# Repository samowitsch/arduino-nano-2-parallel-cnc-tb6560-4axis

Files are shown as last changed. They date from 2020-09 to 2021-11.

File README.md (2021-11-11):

# Arduino nano to parallel TB6560 cnc driver board adapter

This is my little Arduino nano to parallel TB6560 cnc driver board project. Started some time
ago using a red TB6560 4-axis board (before that i had an green 3-axis TB6560). 
At the moment the TB6560 alu case version is my preferred choice 
(but over time i can not remember why the red board was annoying me).
The adapter should also work with 3-axis TB6560 boards if the Pinout is the same.

* [KiCad](https://kicad.org/) files are included if you have special needs.
* Gerber files are included if you want to order your own pcb for e.g. at [jlcpcb.com](https://jlcpcb.com/)
* STL file of simple mount plate made with OpenSCAD is included if you have a 3d printer

Just work in progress current revision 1.4 using GRBL 1.1h.

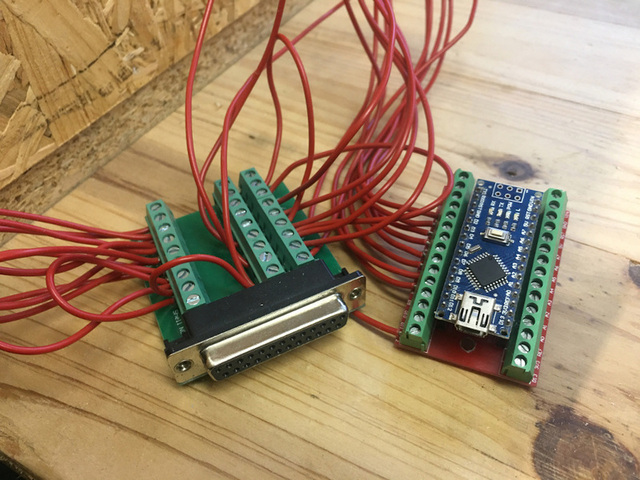
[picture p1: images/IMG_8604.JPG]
First try

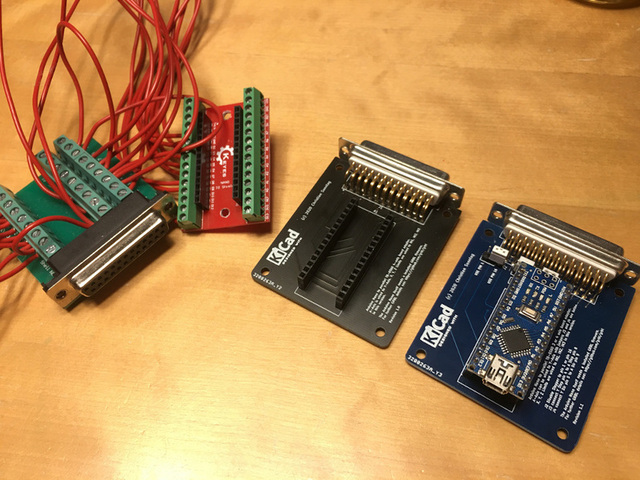
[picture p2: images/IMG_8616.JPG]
Version history

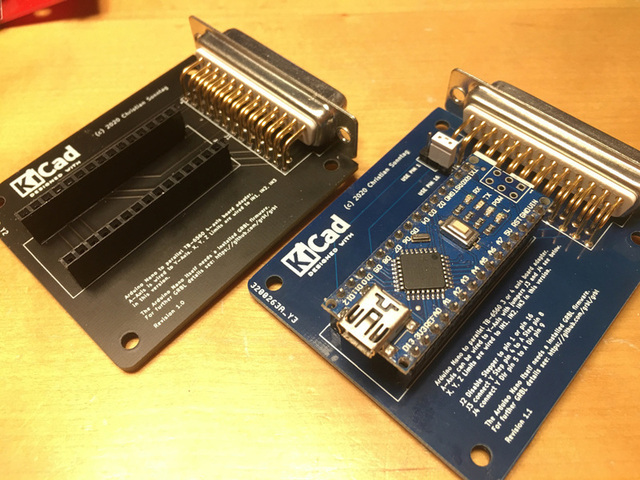
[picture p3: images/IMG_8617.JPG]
Revision 1.0 and 1.1

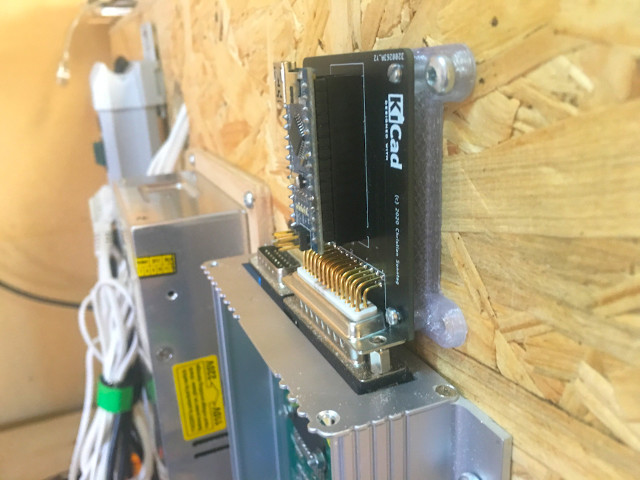
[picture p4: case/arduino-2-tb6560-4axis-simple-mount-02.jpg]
Connected to tb6560 with simple mount

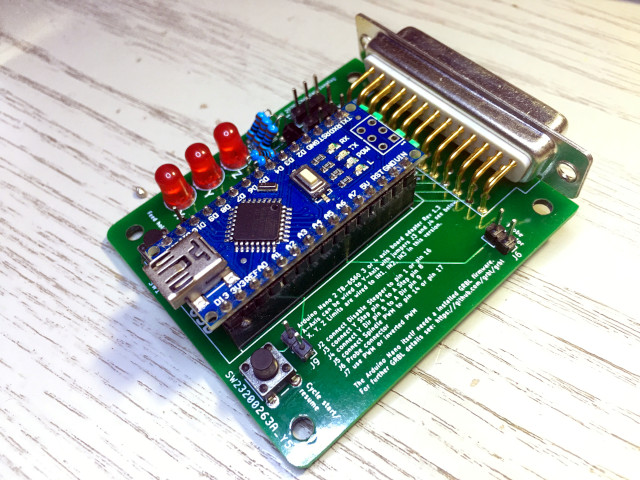
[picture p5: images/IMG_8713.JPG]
Revision 1.3

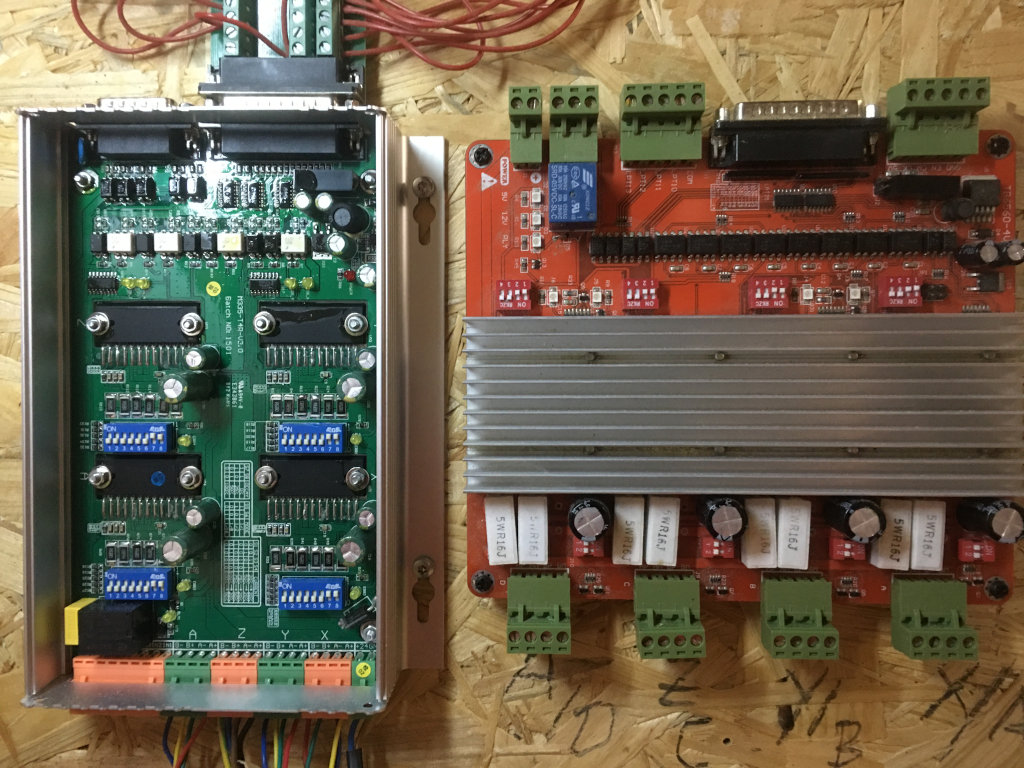
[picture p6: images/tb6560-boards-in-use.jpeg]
Used boards


## Known bugs of rev. 1.3

* holes for resistors are to close for "normal" resistors. my fault this is my first pcb project. i choose a wrong footprint.
* silk outline for X, Y, Z leds on pcb has wrong orientation (my fault or bug in KiCad library?)

## KiCad schema

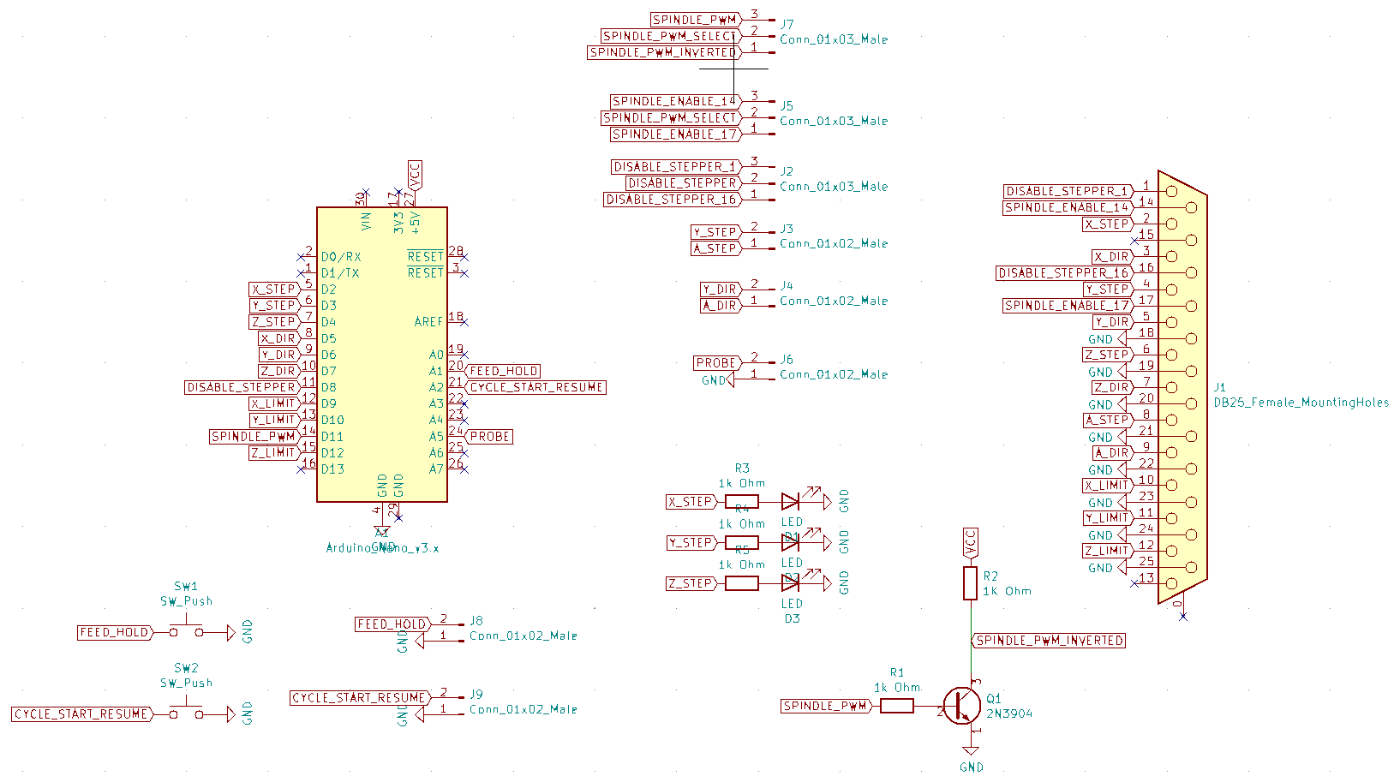
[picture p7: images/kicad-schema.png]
KiCad Schema


## KiCad pcb wiring

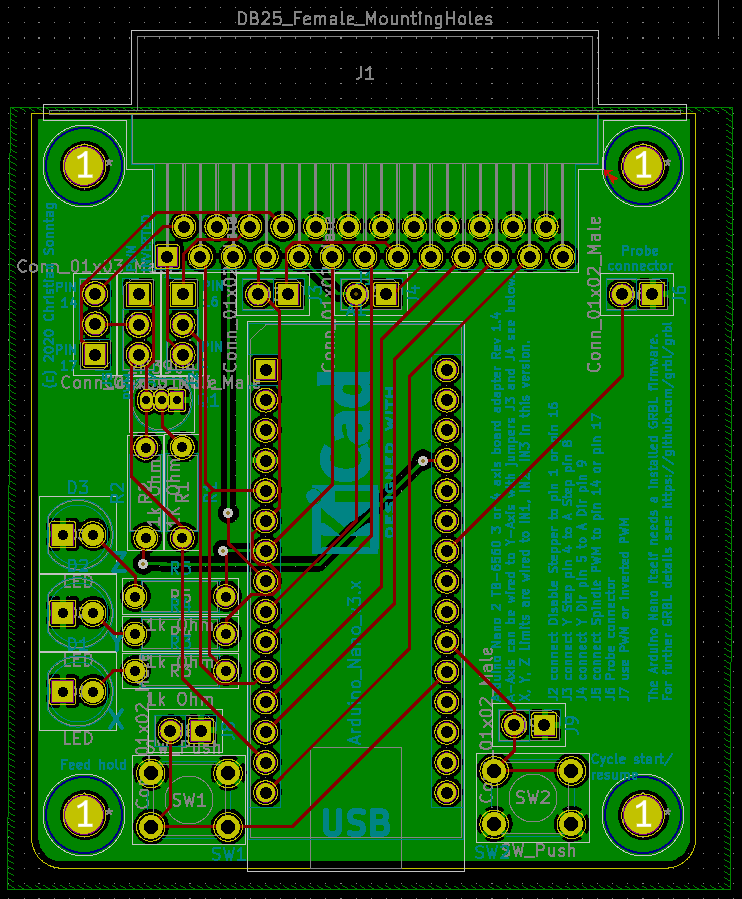
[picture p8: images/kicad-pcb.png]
KiCad pcb wiring


## KiCad pcb 3d preview

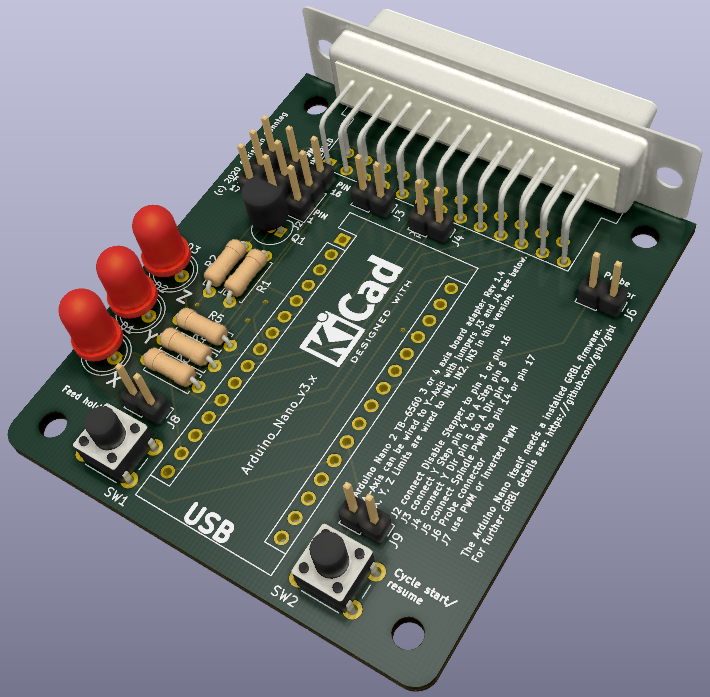
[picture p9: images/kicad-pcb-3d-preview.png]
KiCad pcb wiring


## BOM for revision 1.4

Quantity | Pos | Part
--- | --- | ---
1 | | pcb from pcb manufacturer of your choice
1 | J1 | DSUB-25 female horizontal
5 | R1-R5 | 1k Ohm resistor
1 | Q1 | 2N3904 transistor
2 | SW1,SW2 | tactile push buttons 6x6
3 | D1-D3 | led 5mm
5 | J3,J4,J6,J8,J9 | jumper header 2 pins
3 | J2,J5,J7 | jumper header 3 pins
5 | | jumper
2 | | 15 pin single row female straight header strip 2.54mm pitch for arduino nano

## Simple mount in OpenSCAD

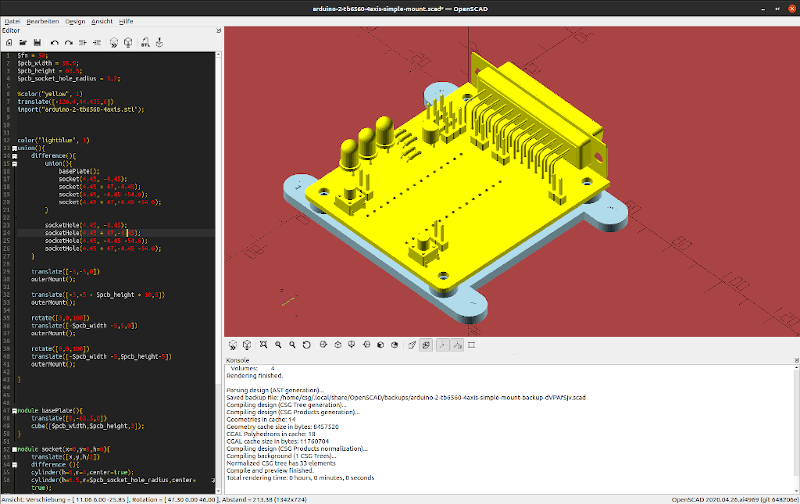
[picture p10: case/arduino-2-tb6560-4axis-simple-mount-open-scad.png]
Simple mount in OpenSCAD


## Revision photos

Picture | Revision | Comment
--- | --- | ---
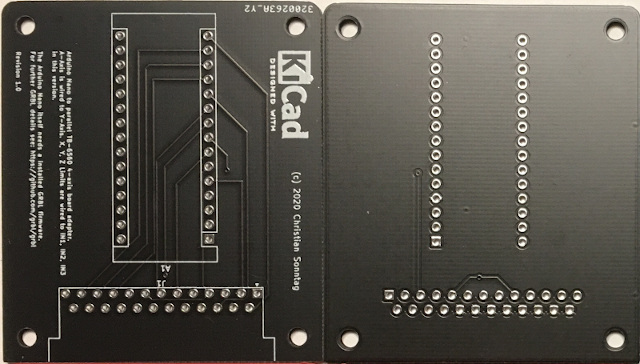
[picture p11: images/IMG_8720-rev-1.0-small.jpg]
 | 1.0 | first dirty revision to get rid of the spaghetti grbl adapter ;o)
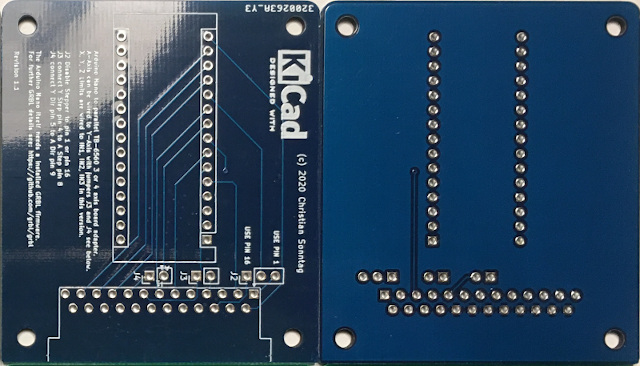
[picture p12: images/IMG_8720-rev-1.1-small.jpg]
 | 1.1 | added jumper headers for the two versions (red pcb, alu case) of the TB6560
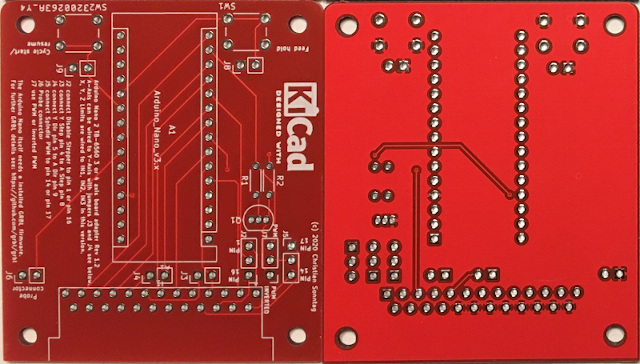
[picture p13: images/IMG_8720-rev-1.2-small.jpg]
 | 1.2 | added two buttons for cycle start/resume and feed hold. added probe connector. added inverter circuit for spindle enable.
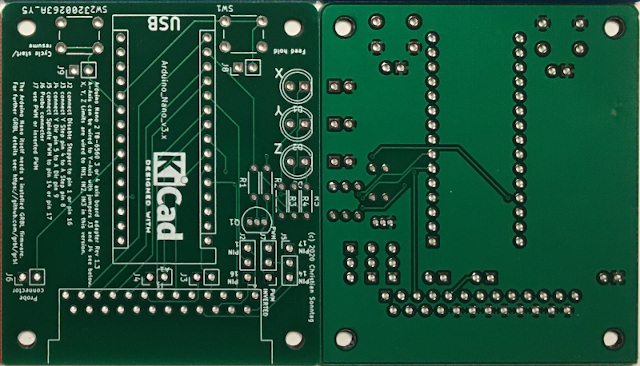
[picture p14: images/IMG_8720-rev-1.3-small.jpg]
 | 1.3 | added leds just for fun.
No real pcb image yet | 1.4 | fix wrong orientation of leds. fix wrong footprint of resistors. reroute affected tracks.

## Pins

Arduino nano | GRBL 1.1 | DB25 red pcb | DB25 alu case version
---|---|---|---
D8 | Disable Stepper | 1 | 16
D2 | X Step | 2 | 2
D3 | Y Step | 4 (+8 A Step) | 4 (+8 A Step)
D4 | Z Step | 6 | 6
D5 | X Dir | 3 | 3
D6 | Y Dir | 5 (+9 A Dir) | 5 (+9 A Dir)
D7 | Z Dir | 7 | 7
D9 | X Limit | 10 (IN1) | 10 (IN1)
D10 | Y Limit | 11 (IN2) | 11 (IN2)
D11 | Spindle Enable | 14 | 17 (see PWM invert!)
D12 | Z Limit | 12 (IN3) | 12 (IN3)
D13 | Spindle Dir | 	 | 
A0 | Reset/Abort | 	 | 
A1 | Feed/Hold | 	 | 
A2 | Cycle Start/Resume | 	 | 
A3 | Cooling Enable | 	 | 
GND | GND | 18-25 | 18-25

## Jumper on board

There are some jumpers to configure the board for the two used 4-axis board versions.

Jumper | Description
---|---
J2 | connect Disable Stepper to pin 1* or pin 16** 
J3 | connect Y Step pin 4 to A Step pin 8
J4 | connect Y Dir pin 5 to A Dir pin 9
J5 | connect Spindle PWM to pin 14* or pin 17**
J6 | Probe connector
J7 | use PWM, inverted PWM or disable (no jumper) 
J8 | connector for alternative feed hold button
J9 | connector for alternative cycle start/resume button

*red board version / **alu case version

## PWM invert

TB6560 boards use low as spindle enable and high as spindel disable (WTF!?). It is the opposite way of how GRBL handle spindle enable/PWM.
The used invert circuit will fix this. But there is a little gap where the invert is not active during startup/shutdown.
> !!! As a workaround for now -> power on arduino at first and power off at last again to prevent injury through spindle.

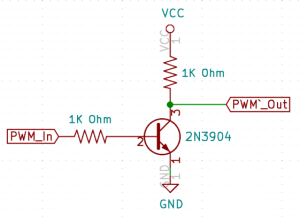
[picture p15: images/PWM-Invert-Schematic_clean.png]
KiCad Schema


Sources: 
* [How to setup inverting PWM signal and using +5v to switch off spindle motor? · Issue #22 · gnea/grbl · GitHub](https://github.com/gnea/grbl/issues/22)
* [GRBL PWM inverter circuit](https://blog.eccentricworkshop.com/grbl-pwm-inverter-circuit/)
* [Explain the Logic NOT Gate or Inverter and its Operation with Truth Table](https://electronicspost.com/explain-the-logic-not-gate-or-inverter-and-its-operation-with-truth-table/)

## My current GRBL settings

```
$$
$0=10
$1=25
$2=0
$3=5
$4=0
$5=0
$6=0
$10=1
$11=0.010
$12=0.002
$13=0
$20=0
$21=0
$22=0
$23=0
$24=25.000
$25=500.000
$26=250
$27=1.000
$30=1000
$31=0
$32=0
$100=402.000
$101=402.000
$102=402.000
$110=1500.000
$111=1500.000
$112=750.000
$120=42.000
$121=42.000
$122=42.000
$130=2000.000
$131=2000.000
$132=2000.000
```

## Probe G Codes

```
G38.2 z-10 f1
```
http://www.linuxcnc.org/docs/2.6/html/gcode/gcode.html#sec:G38-probe
```
G92 z19.2
```
http://www.linuxcnc.org/docs/2.6/html/gcode/gcode.html#sec:G92

## bCNC custom user button

Evaluate gcodes to test with bCNC custom user button.

```text
G38.2 z-100 f5 
G92 z19.7
G0 z50 f600
```

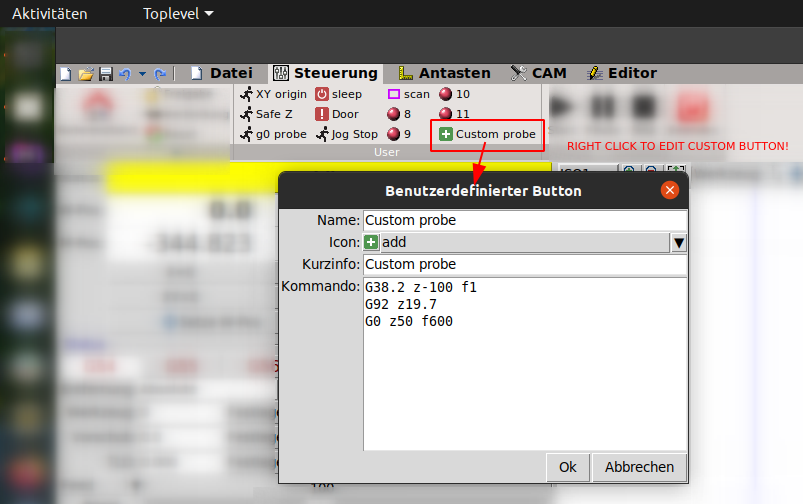
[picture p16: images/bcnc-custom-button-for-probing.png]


## Compiling GRBL

Download, extract and copy GRBL to the Arduino library. More details see here: https://github.com/gnea/grbl/wiki/Compiling-Grbl

Arduino IDE settings:
* Tools -> Board -> "Arduino Nano"
* Tools -> Processor -> "ATmega328P (Old Bootloader)"
* Tools -> Port -> "/dev/ttyUSB0" (may vary)
* Tools -> Programer -> "Atmel-ICE(AVR)"

## Arduino nano pinout

GRBL PWM enabled | GRBL
---|---
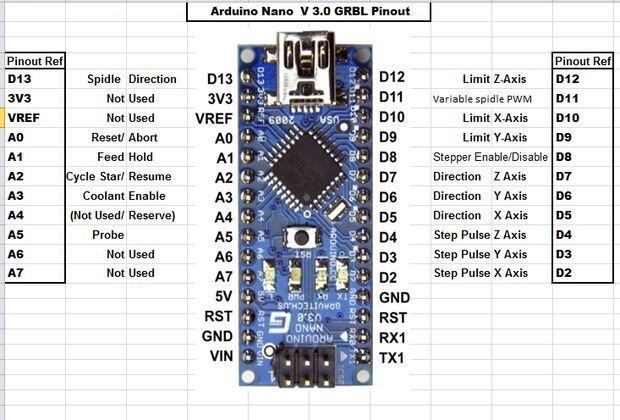
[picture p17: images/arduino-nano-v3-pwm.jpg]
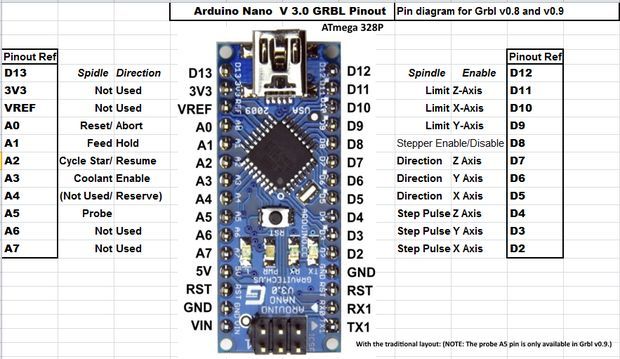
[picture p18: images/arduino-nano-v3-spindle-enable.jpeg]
 | 

### Only for comparison GRBL on STM32F103C8T6 (bluepill)

Just for info. Interesting board with much faster cpu and more memory.  https://github.com/usbcnc/grbl

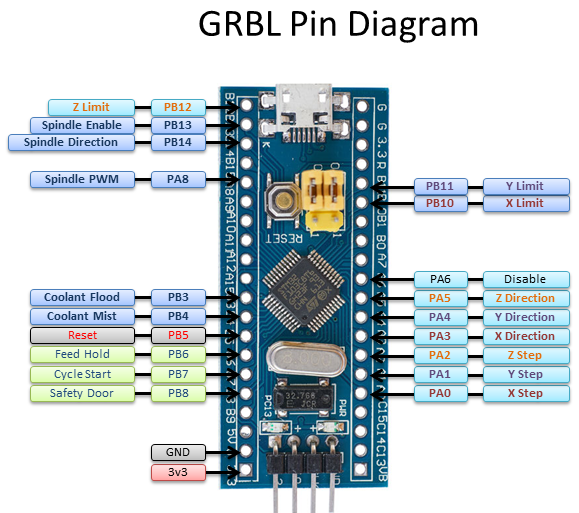
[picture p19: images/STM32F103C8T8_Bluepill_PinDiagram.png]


## other Source
* [Des Fricklers Fräse](https://der-frickler.net/technik/frickelfraese)
* [Make: China-Schrittmotorsteuerung](https://www.heise.de/make/artikel/3-Achs-Schrittmotorsteuerung-aus-China-1518901.html)
* [Grbl CNC USB to TB6560 Interface using Arduino](https://www.coreforge.com/blog/2014/08/grbl-tb6560-interface/)
* [G25 CNC Shield ](http://kclinear.com/G25/Instructions.pdf)

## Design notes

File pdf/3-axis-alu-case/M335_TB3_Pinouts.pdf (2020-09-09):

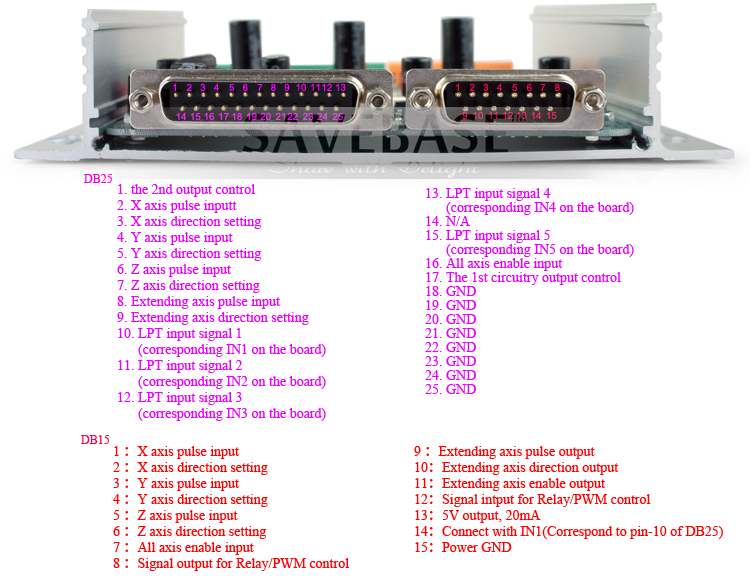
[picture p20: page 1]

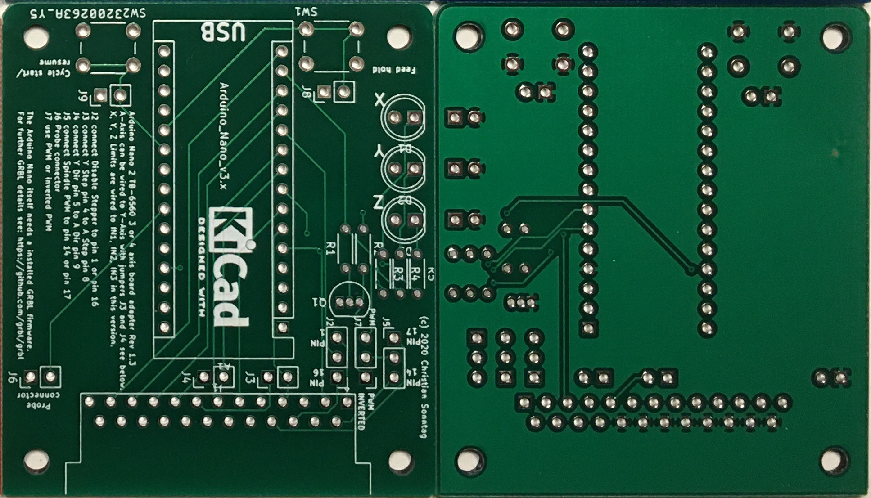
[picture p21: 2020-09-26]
images/IMG_8720-rev-1.3.jpg

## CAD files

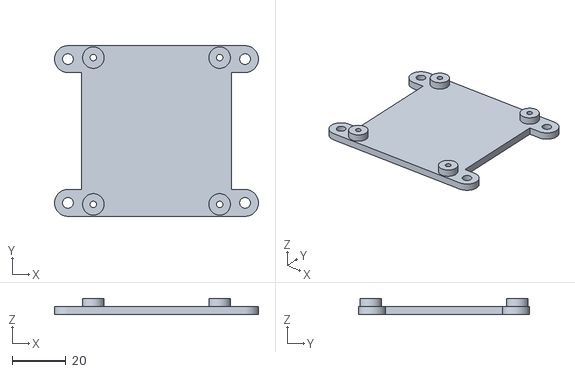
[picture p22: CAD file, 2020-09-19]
case/arduino-2-tb6560-4axis-simple-mount.stl
75.9 x 63.5 x 6.00

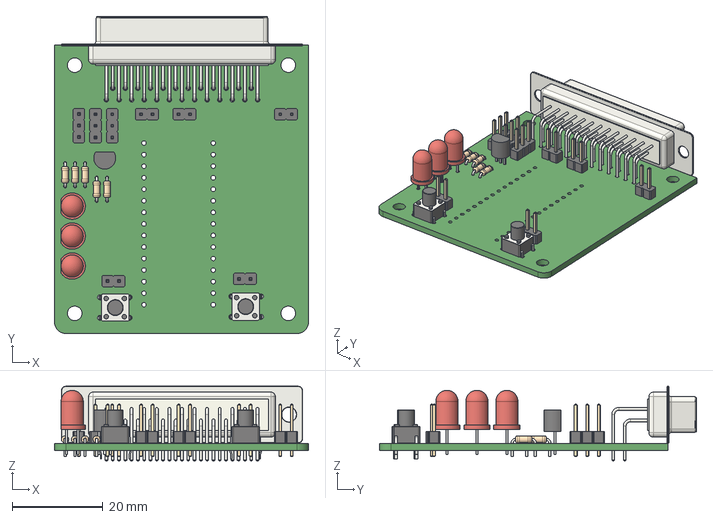
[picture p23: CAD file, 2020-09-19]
case/arduino-2-tb6560-4axis.step
55.9 x 69.8 x 16.4 mm

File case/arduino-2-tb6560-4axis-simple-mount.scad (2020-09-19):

$fn = 50;
$pcb_width = 55.9;
$pcb_height = 63.5;
$pcb_socket_hole_radius = 1.2;

%color("yellow", 1)
translate([-126.4,44.435,6])
import("arduino-2-tb6560-4axis.stl");



color("lightblue", 1)
union(){
    difference(){
        union(){
            basePlate();
            socket(4.45, -4.45);
            socket(4.45 + 47,-4.45);
            socket(4.45, -4.45 -54.6);
            socket(4.45 + 47,-4.45 -54.6);
        }
        
        socketHole(4.45, -4.45);
        socketHole(4.45 + 47,-4.45);
        socketHole(4.45, -4.45 -54.6);
        socketHole(4.45 + 47,-4.45 -54.6);
    }

    translate([-5,-5,0])
    outerMount();

    translate([-5,-5 - $pcb_height + 10,0])
    outerMount();

    rotate([0,0,180])
    translate([-$pcb_width -5,5,0])
    outerMount();

    rotate([0,0,180])
    translate([-$pcb_width -5,$pcb_height-5])
    outerMount();

}



module basePlate(){
    translate([0,-63.5,0])    
    cube([$pcb_width,$pcb_height,3]);
}

module socket(x=0,y=0,h=6){
    translate([x,y,h/2])
    difference (){
    cylinder(h=6,r=4,center=true);
    cylinder(h=6.5,r=$pcb_socket_hole_radius,center=true);
    }
}

module socketHole(x=0,y=0,h=6.5){
    translate([x,y,h/2])
    cylinder(h=h,r=$pcb_socket_hole_radius,center=true);
}

module outerMount(){
    difference(){
        union(){
            translate([0,-5,0])
            cube([5,10,3]);
            cylinder(d=10, h=3);
        }
        cylinder(d=4, h=3);
    }
}

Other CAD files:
case/arduino-2-tb6560-4axis.stl

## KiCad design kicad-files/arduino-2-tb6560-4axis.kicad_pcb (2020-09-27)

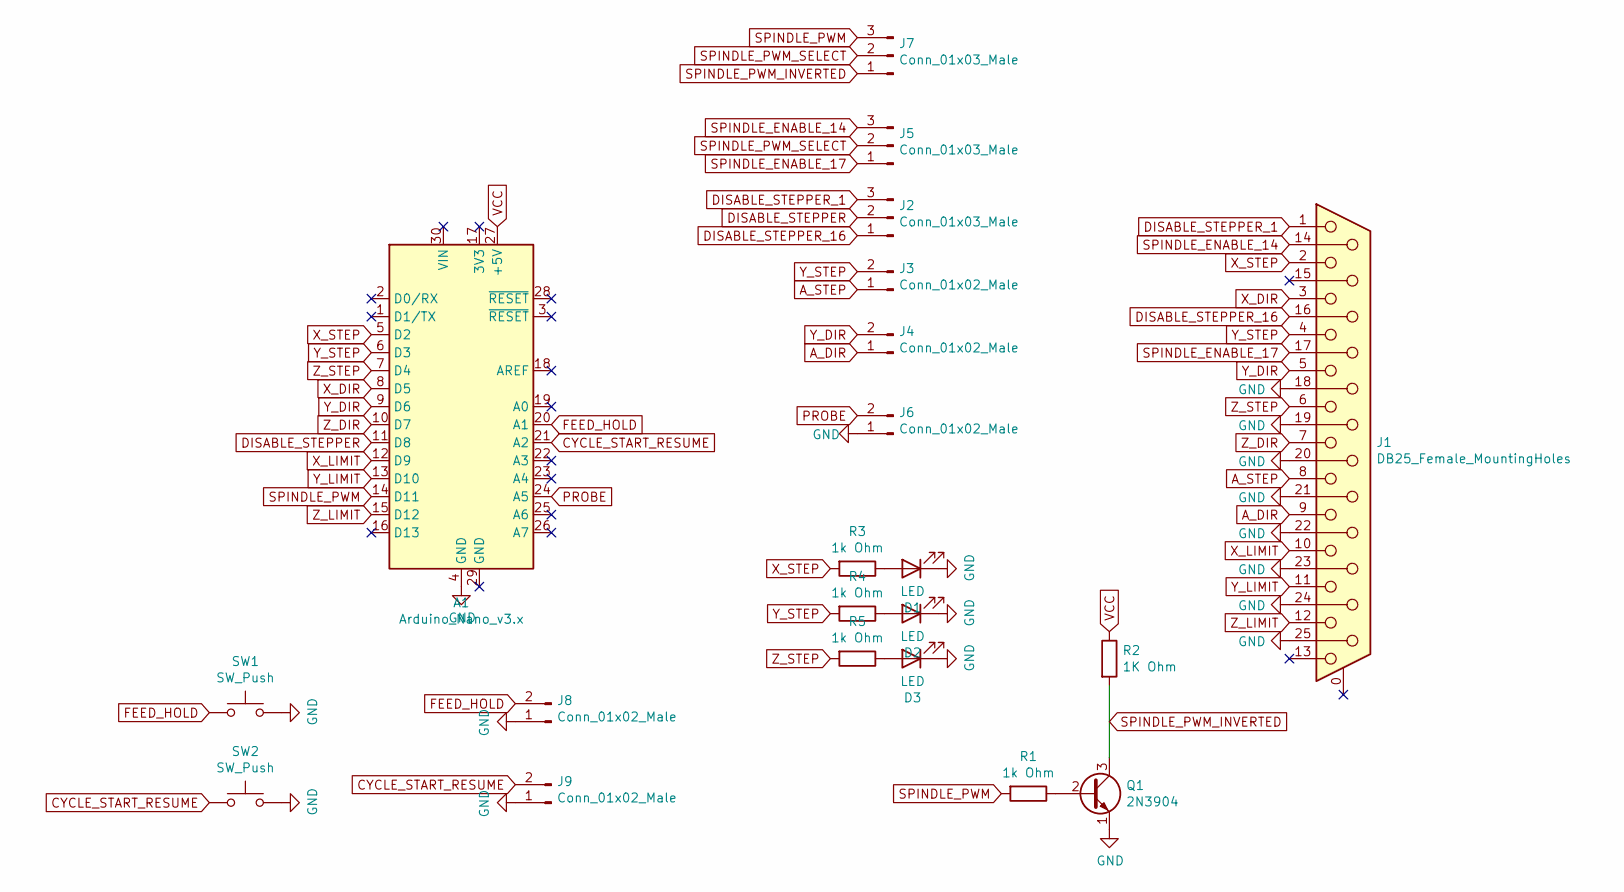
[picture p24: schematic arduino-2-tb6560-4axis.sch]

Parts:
A1: Arduino_Nano_v3.x; Arduino_Nano
D1, D2, D3: LED; LED_D5.0mm
J1: DB25_Female_MountingHoles; DSUB-25_Female_Horizontal_P2.77x2.54mm_EdgePinOffset9.40mm
J2, J5, J7: Conn_01x03_Male; PinHeader_1x03_P2.54mm_Vertical
J3, J4, J6, J8, J9: Conn_01x02_Male; PinHeader_1x02_P2.54mm_Vertical
Q1: 2N3904; TO-92_Inline
R1, R3, R4, R5: 1k Ohm; R_Axial_DIN0207_L6.3mm_D2.5mm_P7.62mm_Horizontal
R2: 1K Ohm; R_Axial_DIN0207_L6.3mm_D2.5mm_P7.62mm_Horizontal
SW1, SW2: SW_Push; SW_PUSH_6mm_H7.3mm

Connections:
A_DIR: J1.9, J4.1
A_STEP: J1.8, J3.1
CYCLE_START_RESUME: A1.21 (A2), J9.2, SW2.1
DISABLE_STEPPER: A1.11 (D8), J2.2
DISABLE_STEPPER_1: J1.1, J2.3
DISABLE_STEPPER_16: J1.16, J2.1
FEED_HOLD: A1.20 (A1), J8.2, SW1.1
GND: A1.4 (GND), D1.1 (K), D2.1 (K), D3.1 (K), J1.18, J1.19, J1.20, J1.21, J1.22, J1.23, J1.24, J1.25, J6.1, J8.1, J9.1, Q1.1 (E), SW1.2, SW2.2
unnamed: D1.2 (A), R3.1
unnamed: D2.2 (A), R4.1
unnamed: D3.2 (A), R5.1
unnamed: Q1.2 (B), R1.1
PROBE: A1.24 (A5), J6.2
SPINDLE_ENABLE_14: J1.14, J5.3
SPINDLE_ENABLE_17: J1.17, J5.1
SPINDLE_PWM: A1.14 (D11), J7.3, R1.2
SPINDLE_PWM_INVERTED: J7.1, Q1.3 (C), R2.2
SPINDLE_PWM_SELECT: J5.2, J7.2
VCC: A1.27 (+5V), R2.1
X_DIR: A1.8 (D5), J1.3
X_LIMIT: A1.12 (D9), J1.10
X_STEP: A1.5 (D2), J1.2, R3.2
Y_DIR: A1.9 (D6), J1.5, J4.2
Y_LIMIT: A1.13 (D10), J1.11
Y_STEP: A1.6 (D3), J1.4, J3.2, R4.2
Z_DIR: A1.10 (D7), J1.7
Z_LIMIT: A1.15 (D12), J1.12
Z_STEP: A1.7 (D4), J1.6, R5.2

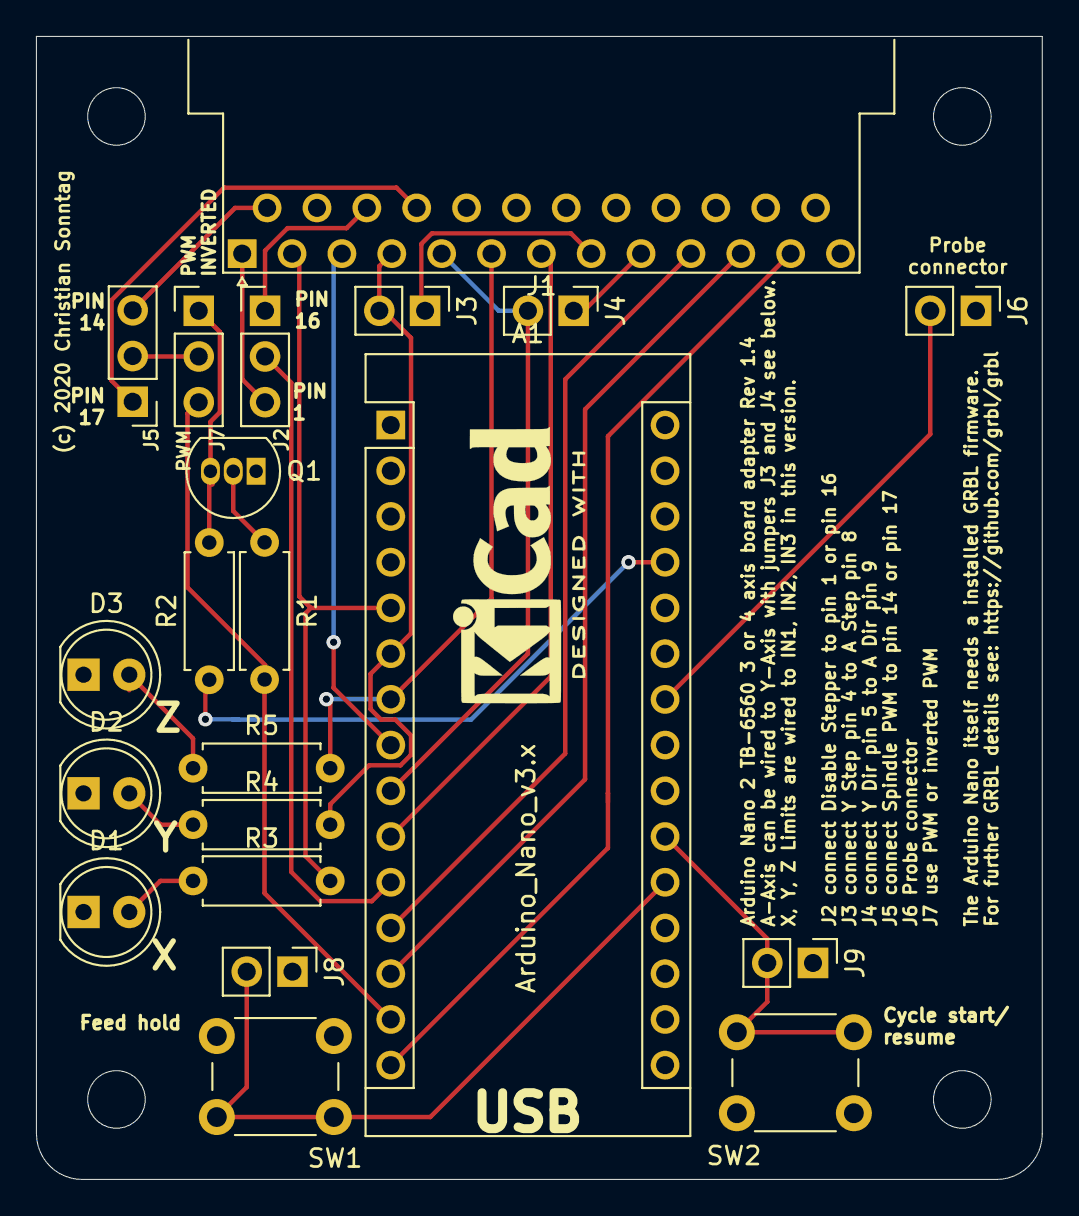
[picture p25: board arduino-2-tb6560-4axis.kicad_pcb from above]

Board: 2 copper layers, 55.9 x 63.5 mm, 21 parts (0 on the bottom side), 28 nets.

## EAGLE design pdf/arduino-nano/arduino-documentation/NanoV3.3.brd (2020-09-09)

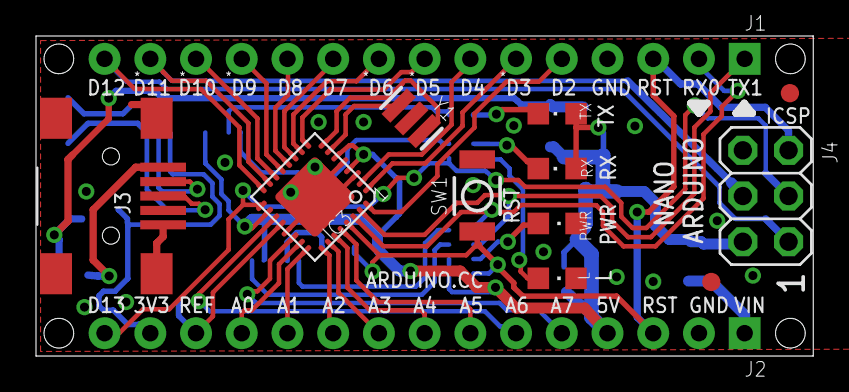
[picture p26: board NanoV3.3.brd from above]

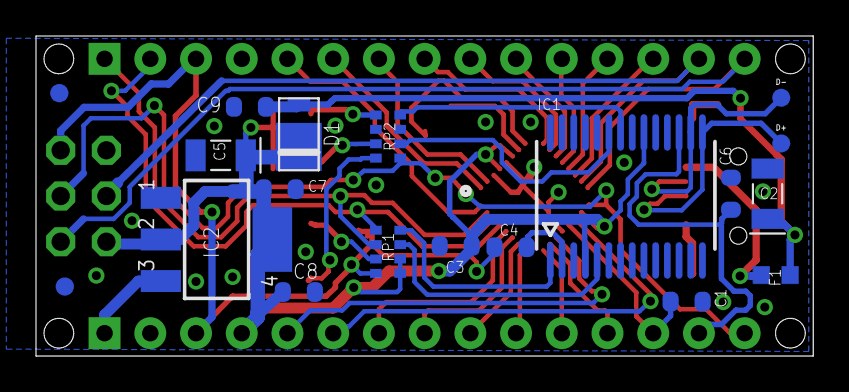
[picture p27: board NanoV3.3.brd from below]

Board: 2 copper layers, 43.2 x 17.8 mm, 33 parts (17 on the bottom side), 43 nets.

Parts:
C1, C4, C6, C9: 100nF; C0603-ROUND
C2, C5: 4,7uF_16V; TAN-A
C3, C7, C8: 1uF; C0603-ROUND
D1: SS1P3L; DO220AAL
D+: DNP; TP-1.00MM
D-: DNP; TP-1.00MM
F1: MFFSMF050; 0603-1608X90N
FRAME1: DNP; FRAME
IC1: FT232RL; SSOP28
IC2: LM1117IMPX-5.0; LINEAR_SOT223
IC3: 328P-MUR; VQFN32
J1, J2: XXXX_STRIPNANO; HEAD15-NOSS
J3: USB-MINI-B_2
J4: 2X03
L: Yellow; CHIPLED_0805
PWR: Green; CHIPLED_0805
RP1, RP2: 1K; CAY16
RX: Red; CHIPLED_0805
SW1: RESET; SMD_157SW
TX: Green; CHIPLED_0805
U$4, U$5, U$53, U$54: DNP; FD-1-1.5
Y1: 16MHz; RESONATOR

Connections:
3V3: C6.2, IC1.17, J2.14
+5V: C3.1, C5.1, C7.1, C8.1, D1.P$1, IC1.4, IC1.20, IC2.2, IC2.4, IC3.4, IC3.6, IC3.18, J2.4, J4.2, RP1.5, RP1.6, RX.A, TX.A
A0: IC3.23, J2.12
A1: IC3.24, J2.11
A2: IC3.25, J2.10
A3: IC3.26, J2.9
A4: IC3.27, J2.8
A5: IC3.28, J2.7
A6: IC3.19, J2.6
A7: IC3.22, J2.5
AREF: C1.1, IC3.20, J2.13
COM: C1.2, C2.2, C3.2, C5.2, C6.1, C7.2, C8.2, C9.2, IC1.7, IC1.18, IC1.21, IC1.25, IC1.26, IC2.1, IC3.3, IC3.5, IC3.21, IC3.33, J1.4, J2.2, J3.1, J3.6, J3.7, J3.8, J3.9, J4.6, L.C, PWR.C, RP2.3, RP2.6, SW1.1, Y1.2
D0/RX: IC3.30, J1.2, RP1.1
D1/TX: IC3.31, J1.1, RP1.2
D2: IC3.32, J1.5
D3: IC3.1, J1.6
D4: IC3.2, J1.7
D5: IC3.9, J1.8
D6: IC3.10, J1.9
D7: IC3.11, J1.10
D8: IC3.12, J1.11
D9: IC3.13, J1.12
D10: IC3.14, J1.13
D11/MOSI: IC3.15, J1.14, J4.4
D12/MISO: IC3.16, J1.15, J4.1
D13/SCK: IC3.17, J2.15, J4.3, RP2.1
unnamed: IC3.8, Y1.3
unnamed: IC3.7, Y1.1
unnamed: PWR.A, RP1.3
unnamed: C4.2, IC1.2
unnamed: D+.X, IC1.15, J3.3
unnamed: D-.X, IC1.16, J3.4
unnamed: L.A, RP2.8
unnamed: IC1.23, RP2.2
unnamed: IC1.22, RP2.4
unnamed: RP2.5, TX.C
unnamed: F1.2, J3.5
unnamed: RP2.7, RX.C
RESET: C4.1, IC3.29, J1.3, J2.3, J4.5, RP1.4, SW1.2
RX: IC1.1, RP1.8
TX: IC1.5, RP1.7
VIN: IC2.3, J2.1
VUSB: C2.1, C9.1, D1.P$2, F1.1

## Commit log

2020-09-09 Update .gitignore, README.md, and 97 more files...
    [NanoV3.3.brd, NanoV3.3.sch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]
2020-09-11 added push buttons and jumper header for feed hold and cycle start/resume.
    [arduino-2-tb6560-4axis-B_Cu.gbr, arduino-2-tb6560-4axis-B_Mask.gbr, arduino-2-tb6560-4axis-B_Paste.gbr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]
2020-09-12 more ideas for rev 1.3
    [arduino-2-tb6560-4axis-B_Cu.gbr, arduino-2-tb6560-4axis-B_Mask.gbr, arduino-2-tb6560-4axis-B_Paste.gbr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]
2020-09-19 changed readme. added simple mount created with OpenSCAD.
    [arduino-2-tb6560-4axis-simple-mount.scad, arduino-2-tb6560-4axis-simple-mount.stl, arduino-2-tb6560-4axis.step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]
2020-09-26 added pcb pictures. add note for bCNC custom user button for probing. added some pdfs.
2020-09-27 add BOM
2020-09-27 rev. 1.4. fix wrong led orientation. fix wrong resistor footprint. reroute affected tracks.
    [arduino-2-tb6560-4axis-B_Cu.gbr, arduino-2-tb6560-4axis-B_Mask.gbr, arduino-2-tb6560-4axis-B_Paste.gbr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]
2021-11-10 Update README.md
    https://forum.kicad.info/t/warning-avoid-all-links-to-kicad-pcb-org-use-kicad-org/31521
2023-09-18 add GRBL 1.1 configuartion doc
2023-09-18 add GRBL 1.1 commands doc

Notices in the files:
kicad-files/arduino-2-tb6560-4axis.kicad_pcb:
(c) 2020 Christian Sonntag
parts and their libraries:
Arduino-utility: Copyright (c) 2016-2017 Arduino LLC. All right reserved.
